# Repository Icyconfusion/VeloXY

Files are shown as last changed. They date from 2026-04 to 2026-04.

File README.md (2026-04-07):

# VeloXY
A CoreXY 3d printer with a heated chamber and bed. It has 300x300x320 print volume and 3 point bed-levelling. I made this project to be able to print higher quality materials. The printer runs Marlin firmware.



## **Assembly**
The assembly is centered around a frame made of galvanised square steel (40x40). The frame is essentially a cube, where the square steel is welded together, so no connectors are needed. Two cross bars at the top are lowered by ~60mm to provide clearance for the extruder and filament path. 



Components are mounted onto the square steel using rivet nuts. 

### Z axis

The Z axis uses 3 independent motors to enable 3 point bed-levelling. At each motor, there is a T8 leadscrew to drive motion, and an 8mm smooth rod for support. The smooth rod is press fit into the 3d printed brackets through small slits in the brackets for compliance. The nema 17 motor mounts to the bracket, and secures the leadscrew with a 5x8 shaft coupler. At the idler, the leadscrew is held in place with a 16x8x5 bearing, allowing rotation. 






The intersection of the corner Nema 17 motors with the square steel is not an error, as a section of the square steel will be cutout (a rectangle just bigger than the motor) so that the motor sits in there without touching any of the steel.

Bed supports hold an LM8UU bearing and a anti-backlash nut. This transfers motion to the bed. The bed sits on these supports through a threaded steel ball (Vcore system) which rests on metal dowels in the bracket.







### Gantry (X and Y)
The gantry is the 2020 T slot profile that moves back and forth along the Y axis. The gantry is supported by two 3d printed brackets, one at each end, that connect it to the MGN12H carriages. The Y linear rails are mounted on the underside of the frame.




 The gantry has a linear rail along the top face of the profile, this is the X axis.

 
 

The extruder runs along this linear rail for the X axis. The extruder is sat on a MGN12H carriage, and holds a nema 17 motor for the extruder and the hotend. Two blower fans cool the nozzle/part.





### Chamber
The chamber is mounted around the frame, aiming to create a closed off area that can be heated for better printing. The enclosure is made up of ACM, mounted on the top, back, bottom and sides using rivet nuts.


A hole is drilled in the back panel so that wires for electronics can enter the chamber.



The enclosure is finished with a polycarbonate door on a hinge mounted to the frame, with a 3d printed handle.



The chamber is heated by a PTC heater in the bottom corner, mounted to a base tube of square steel, and a vertical post using a small metal rectangle with mounting holes drilled.




### Motion
The printer is based on a coreXY motion system. The belts are stacked on top of each other, so there is no need for a crossover system.



There are pulleys on the idlers and belt post on the gantry. The belts connect to a post/screw on the extruder.



## **Electronics**
I designed a PCB motherboard around the mega2560 that will control the printer. The motherboard is 2 layers and uses A4988 footprint drivers. Power for the motors and heaters enters the board with a screw terminal from the 24v 600w PSU. There is also an 5v screw terminal input which powers the motor driver logic, lcd and if needed the arduino. The 5v comes from the psu but with a buck converter between. There is a third power input for the arduino vin pin which can be used if needed, but the arduino can also be powered by the 5v supply and usb. The LCD connects to a 4 pin header, with RX, TX, 5V and GND. All three heaters (Hotend, bed and chamber) are controlled through TO-220 mosfets, but the chamber has its own PSU. There are also fuses for the power inputs.





## **BOM**
**Printed parts**
| Part | Quantity | Picture |
|---|---|---|
| A bottom corner | 1 |
| A bed support | 1 | 
| A idler | 1 |
| A motor | 1 | 
| A gantry belt post | 1 |
| A gantry mount | 1 | 
| B bottom corner | 1 | 
| B bed support | 1 |
| B idler | 1 | 
| B motor | 1 | 
| B gantry belt post | 1 | 
| B gantry mount | 1 | 
| Z front bracket | 1 |
| Front bed support | 1 | 
| Front top support | 1 | 
| Handle | 1 | 
| Extruder | 1 | 
| Electronics case | 1 | 

**Purchased Parts**
|Name |Purpose |Quantity|Total Cost (USD)|Link |Distributor |
|---|---|---|---|---|---|
|Mosfets |IRLB3034PBF MOSFETs for controlling the heaters of the printer. |3 |4.06 |https://www.aliexpress.com/item/4000222160431.html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 |Aliexpress |
|Capacitors |220 uf 50V capacitors for the motherboard |6 |3.80 |https://www.aliexpress.com/item/1005011631970768.html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 |Aliexpress |
|female headers |For connecting the A4988 drivers to the motherboard |12 |5.52 |https://www.aliexpress.com/item/4000059515638.html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 |Aliexpress |
|Male pin headers |For connecting components like endstops and the MCU to the motherboard |1 |8.74 |https://www.aliexpress.com/item/1005011692961056.html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|Aliexpress |
|Blower fan |Cooling the nozzle/part |2 |4.60 |https://www.aliexpress.com/item/1005006744255466.html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 |Aliexpress |
|Bearing |16x8x5 bearing for holding the top of leadscrews in place |3 |0.45 |https://jlcmc.com/product/b/C15/BR8364/deep-groove-ball-bearing-double-side-with-dust-cover |JLCMC |
|Fuse |KCD3 Fuse holder for the motherboard. For the main PSU, 30-35A fuse. For bed PSU, 20A fuse. |2 |7.80 |https://www.aliexpress.com/item/1005005182079397.html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 |Aliexpress |
|Screw terminals  |30A Screw terminals for powering motherboard, and connecting heaters to motherboard |7 |5.52 |https://www.aliexpress.com/item/1005009941526260.html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 |Aliexpress |
|Resistors |1/4 watt, 10k and 150 ohm resistors for the motherboard MOSFETS |6 |5.73 |https://www.aliexpress.com/item/1005008464765307.html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 |Aliexpress |
|Capacitors |100 nf (0.1 uf) 50V ceramic capacitors for the motherboard |6 |0.00 |https://www.aliexpress.com/item/1005006883576409.html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 |Aliexpress |
|Screws |For fastening components to the the rivet nuts. 225 M5, 5 M4, 100 M3 |330 |7.73 |https://jlcmc.com/product/s/E02/EDLA/hex-socket-screw-full-partial-thread-standard-type-(din-912-gb-t-70.1) |JLCMC |
|PEI sheet |The print surface that goes on top of the print bed. 310x310 |1 |14.63 |https://www.aliexpress.com/item/1005006866749353.html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 |Aliexpress |
|Polycarbonate |Polycarbonate sheet for the door. |1 |30.00 |https://www.bunnings.com.au/suntuf-400-x-400-x-8mm-clear-palsun-polycarbonate-sheet-8mm_p1010483 |Bunnings |
|Heat set inserts |Attaching electronics case lid |4 |0.17 |https://jlcmc.com/product/s/E04/EMLU/insert-nut-through-hole |JLCMC |
|Rivet nuts |Nuts for fastening things to the square steel tubing. Need 175 M5, 5 M4, 100 M3 |280 |7.59 |https://jlcmc.com/product/s/E12/EMJE/rivet-nut-pull-through-ribbed-dome-head |JLCMC |
|MK8 extruder |The MK8 extruder pushes filament into the hotend using the Nema 17 motor |1 |4.33 |https://www.aliexpress.com/item/1005007542803374.html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 |Aliexpress |
|PTC heater |The space heater for the heated chamber of the printer to enable printing harder materials. 24v 400w. |1 |17.00 |https://www.aliexpress.com/item/1005007442989854.html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 |Aliexpress |
|Heated bed |300x300 24v heated bed to heat up the print surface |1 |25.00 |https://www.aliexpress.com/item/1005008233590835.html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 |Aliexpress |
|Square steel tube|2mm thick 40x40 Galvanised square steel tubing is the frame for the printer. I will use 40x40 as it has greater strength. I will cut it to length, drill holes where necessary for mounting and then weld together. I will need 6m. |1 |31.06 |https://www.rhssteelsupplies.com.au/hikashop-menu-for-categories-listing/product/3127-galvanised-square-hollow-box-section-40-x-40-x-2-5-gal-8-metres.html |RHS Steel Supplies|
|ACM panel |ACM panel will make the enclosure for the printer. I need to use ACM as it is the cheapest suitable material, as it must be able to contain the heat of the chamber without weakening. I will cut/bend the ACM to fit around the frame.|1 |60.00 |https://plastix.com.au/product/aluminium-composite-panels/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 |Plastix.com.au |

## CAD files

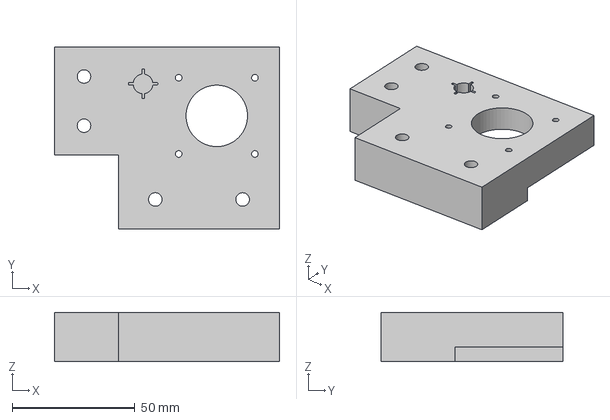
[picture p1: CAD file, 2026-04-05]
CAD/A+corner+bracket.stp
91.5 x 74.0 x 20.0 mm

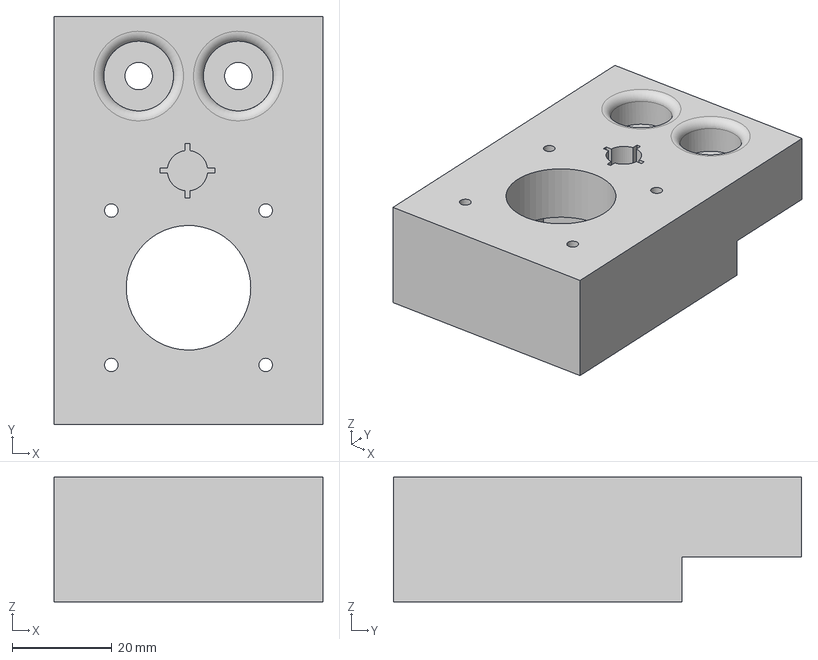
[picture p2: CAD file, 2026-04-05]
CAD/Z+front+bracket.stp
54.0 x 82.0 x 25.0 mm

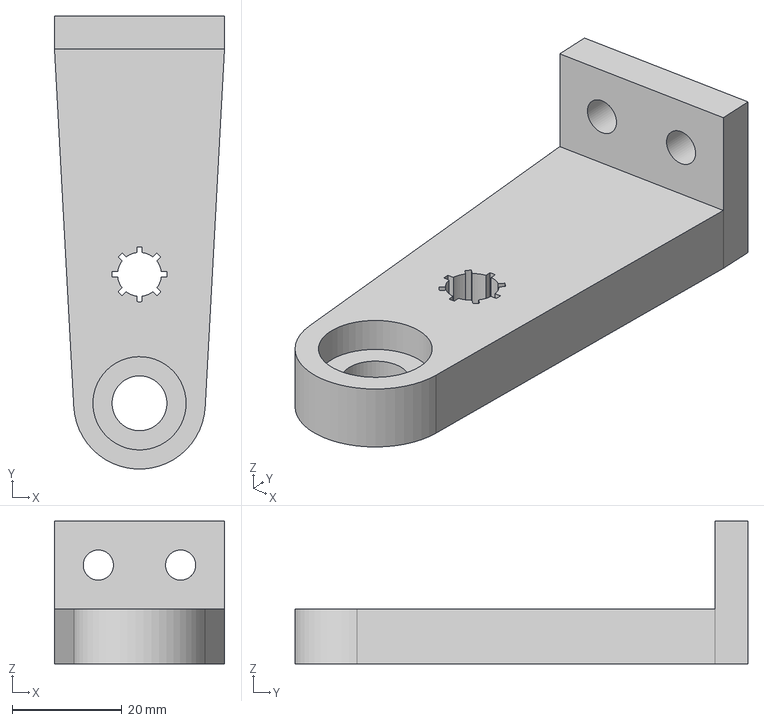
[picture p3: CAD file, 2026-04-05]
CAD/Front+top+support.stp
31.0 x 82.6 x 26.0 mm

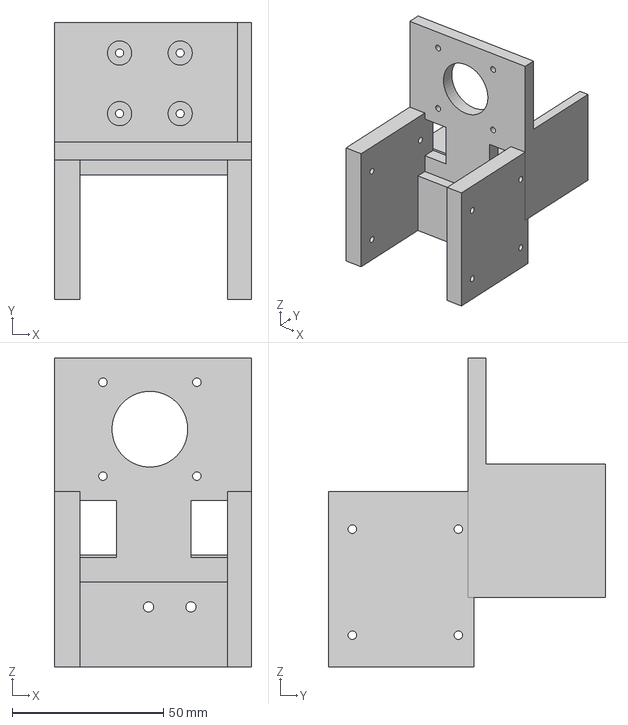
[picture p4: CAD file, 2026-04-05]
CAD/X+carriage.stp
65.0 x 91.3 x 102.0 mm

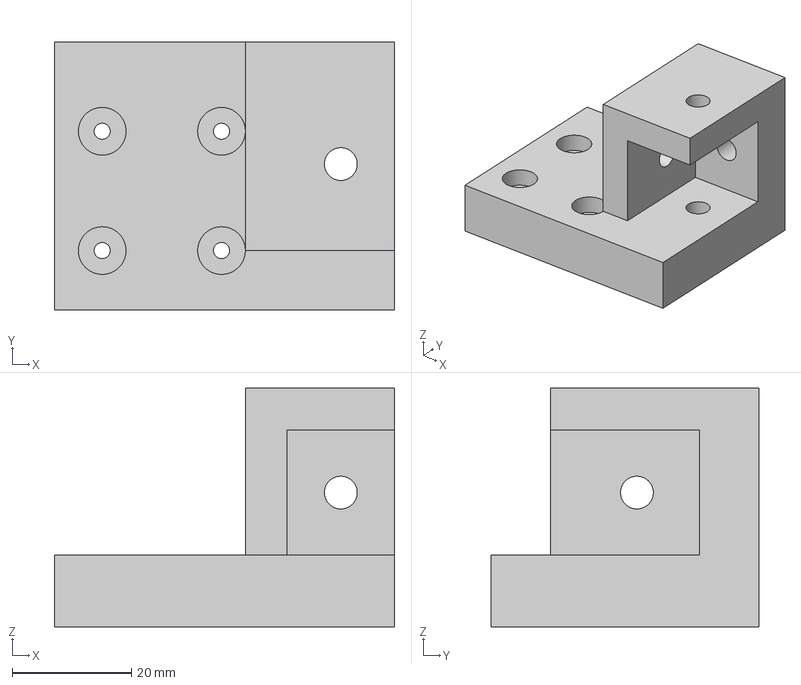
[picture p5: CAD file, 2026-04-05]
CAD/Y+carriage+A.stp
57.0 x 45.0 x 40.0 mm

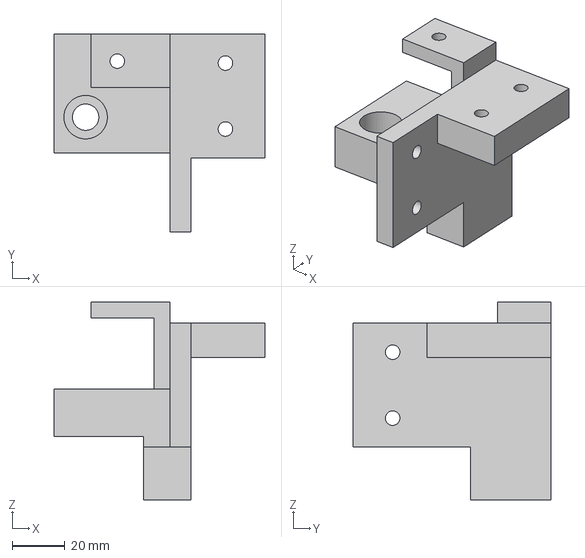
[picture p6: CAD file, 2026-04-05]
CAD/B+idler.stp
80.0 x 75.0 x 75.0 mm

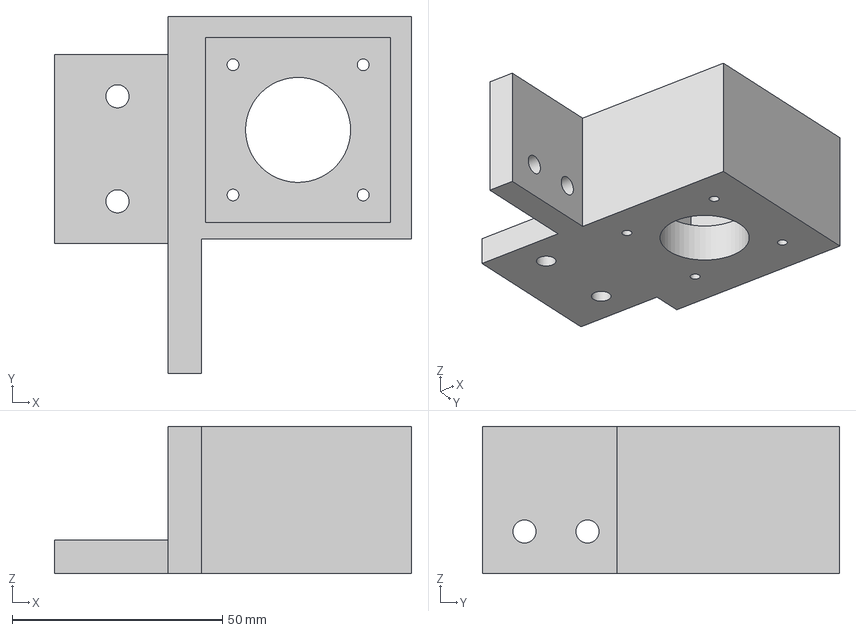
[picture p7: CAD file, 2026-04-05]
CAD/B+motor.stp
85.0 x 85.0 x 35.0 mm

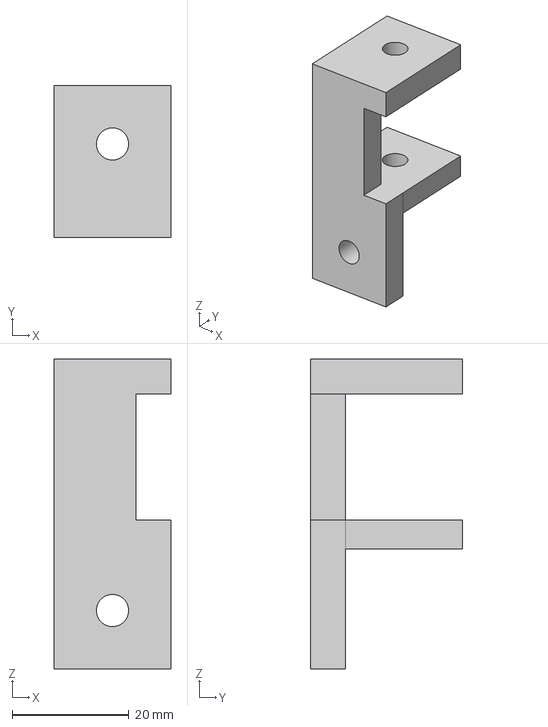
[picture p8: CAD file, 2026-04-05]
CAD/Gantry+belt+post.stp
20.0 x 26.0 x 53.0 mm

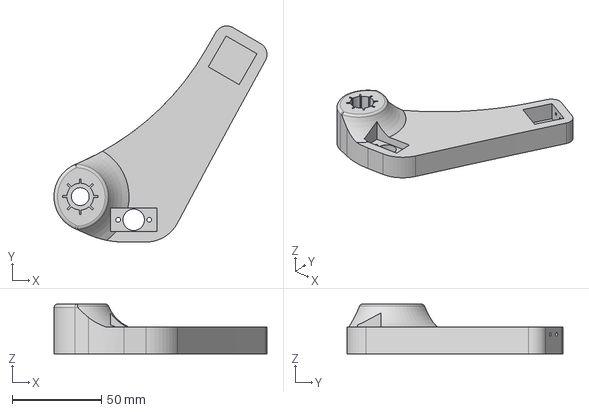
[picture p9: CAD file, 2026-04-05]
CAD/A+bed+support.stp
119.5 x 121.3 x 28.0 mm

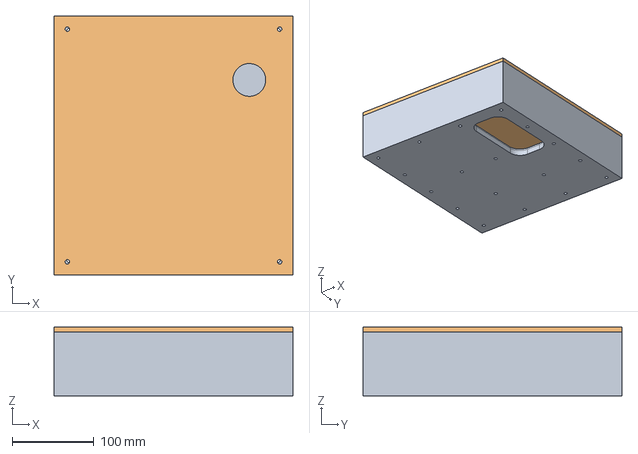
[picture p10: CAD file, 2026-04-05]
CAD/Electronics+case.stp
291.0 x 316.0 x 84.0 mm

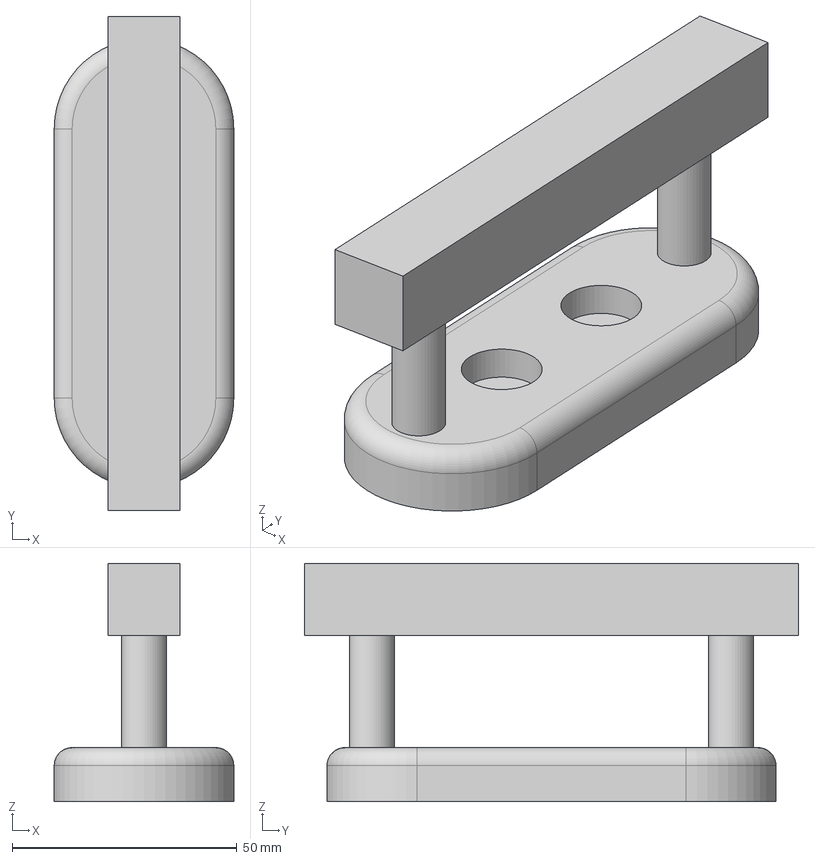
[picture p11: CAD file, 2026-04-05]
CAD/Handle.stp
40.0 x 110.0 x 53.0 mm

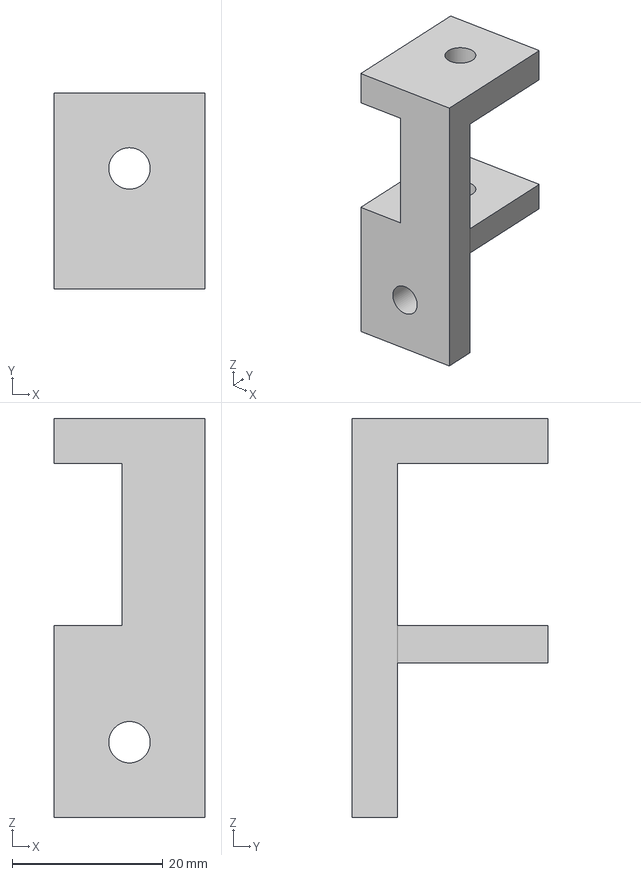
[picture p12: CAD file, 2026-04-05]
CAD/Gantry+belt+post+B.stp
20.0 x 26.0 x 53.0 mm

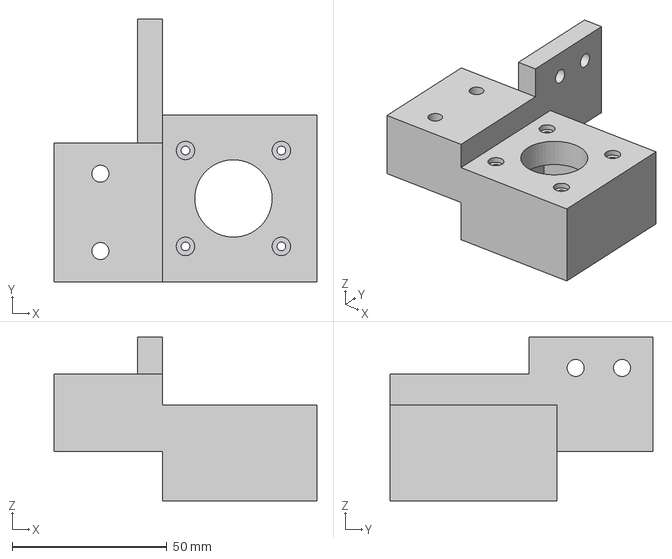
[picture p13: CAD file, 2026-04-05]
CAD/A+motor.stp
85.0 x 85.0 x 53.0 mm

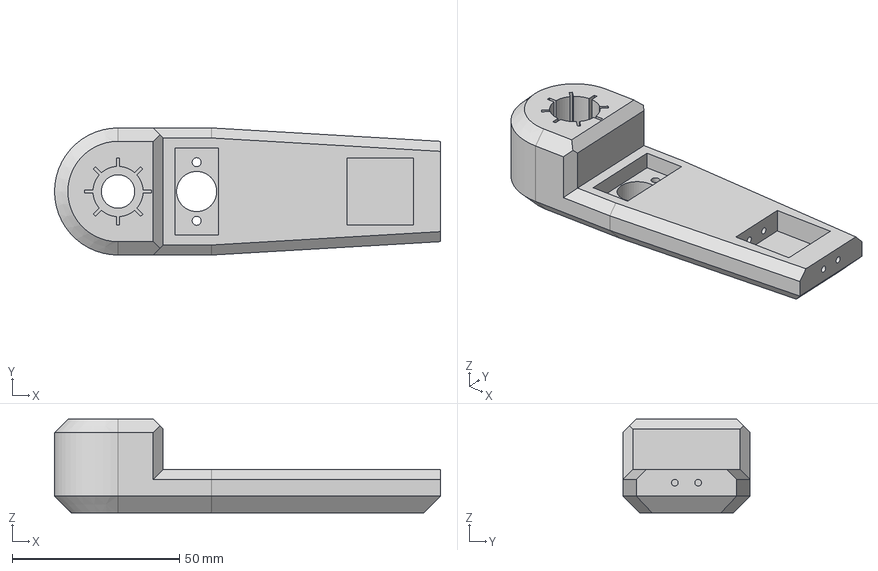
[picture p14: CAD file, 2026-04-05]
CAD/Bed+support+rear.stp
115.4 x 38.0 x 28.0 mm

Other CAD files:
CAD/Assembly (1).stp
CAD/B+corner+bracket.stp
CAD/Y+carriage+B.stp
CAD/B+bed+support+new.stp
CAD/A+idler.stp

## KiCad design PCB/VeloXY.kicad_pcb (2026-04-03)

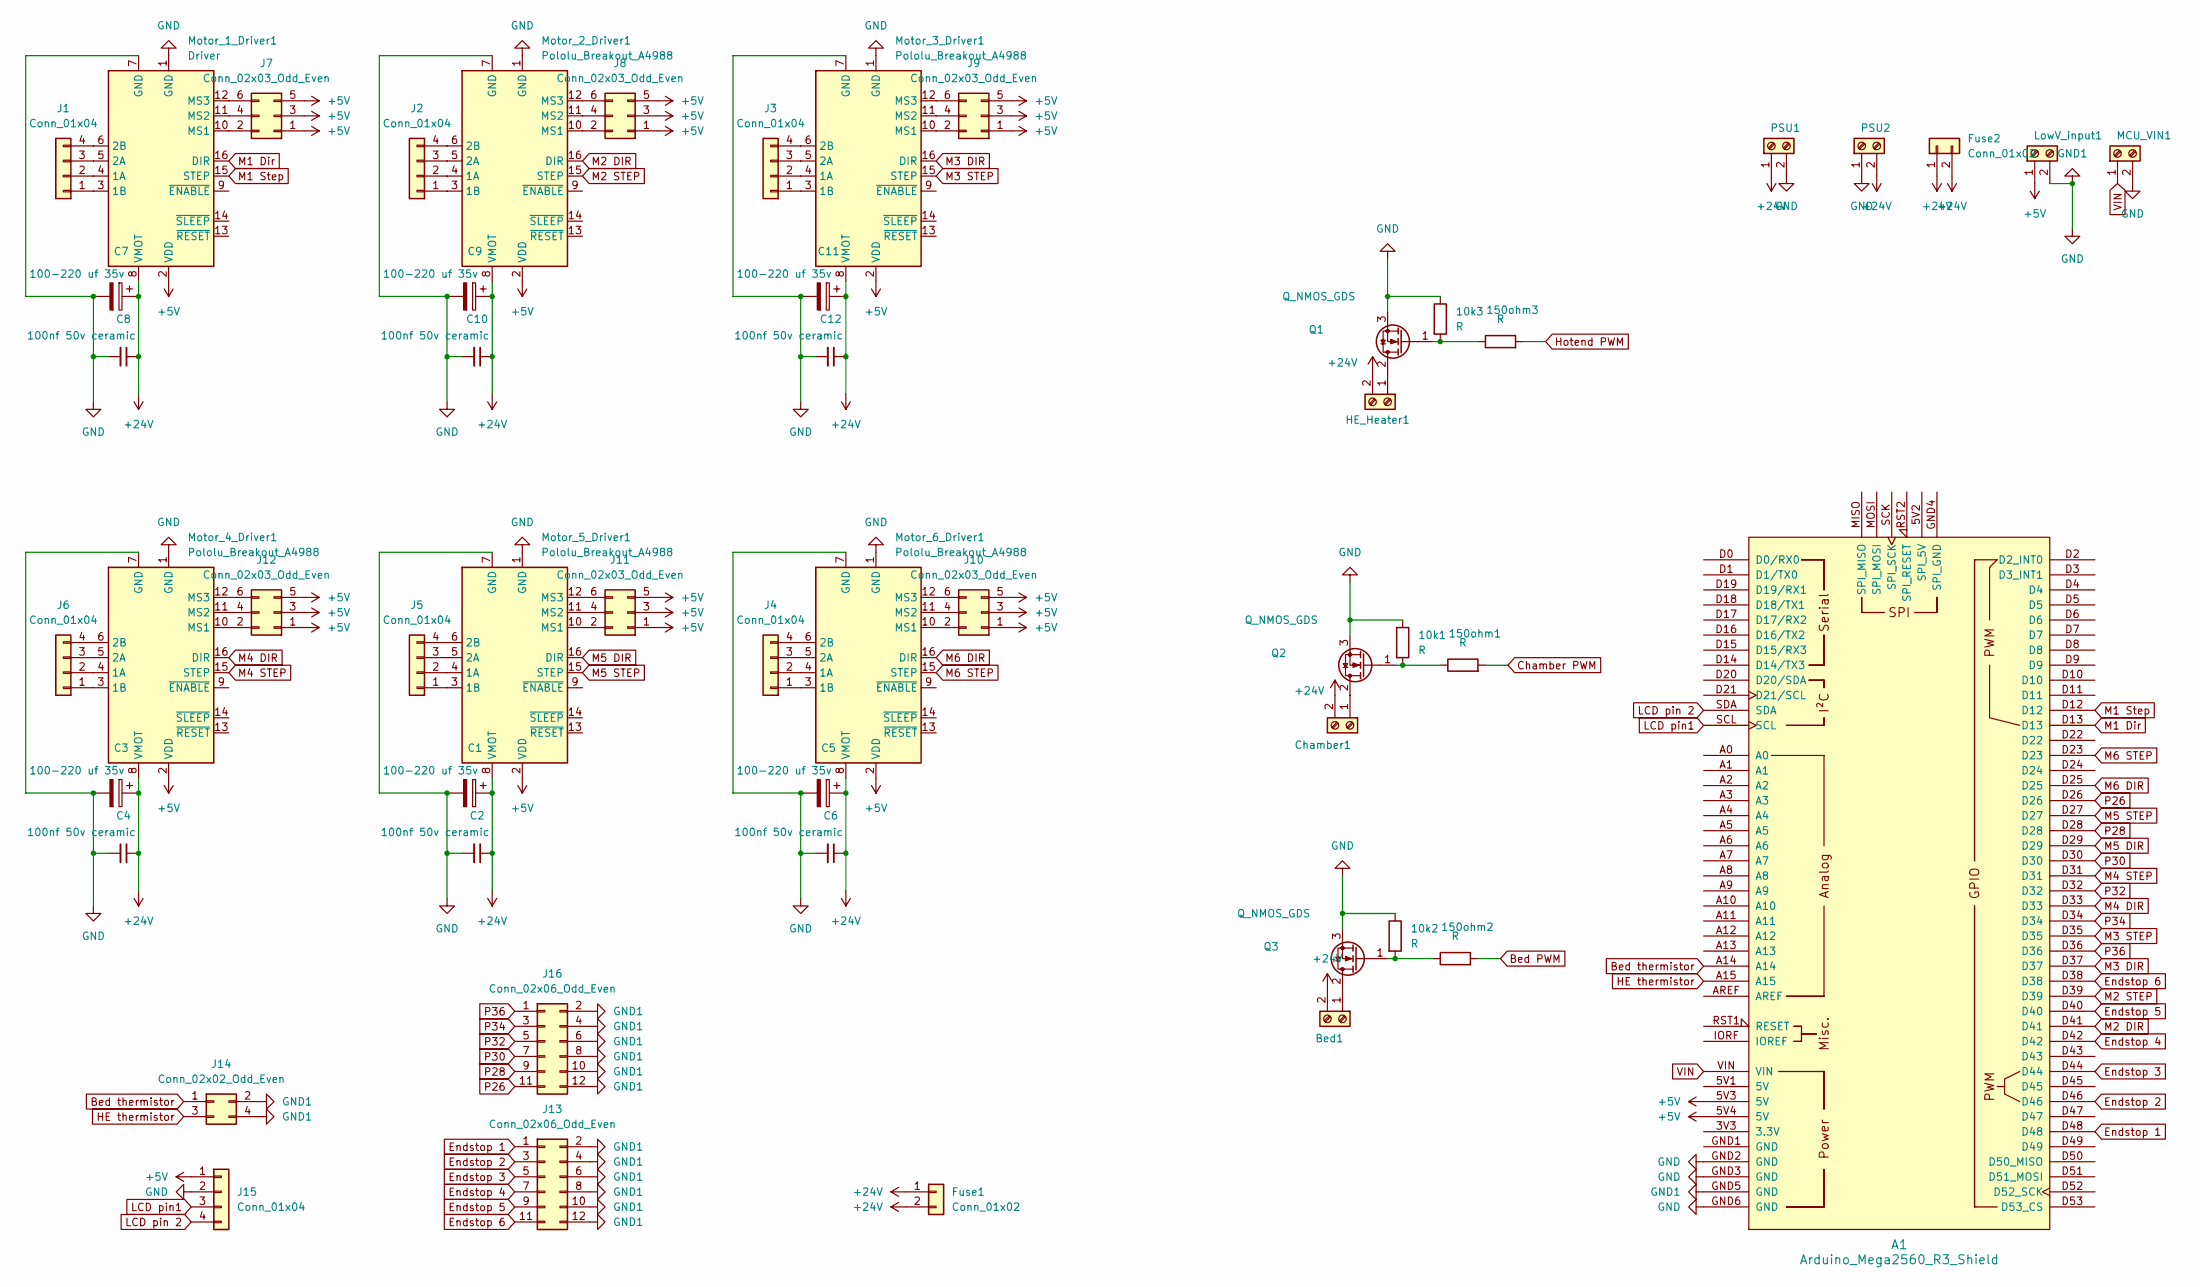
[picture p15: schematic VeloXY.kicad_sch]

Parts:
10k1, 10k2, 10k3, 150ohm1, 150ohm2, 150ohm3: R; R_Axial_DIN0207_L6.3mm_D2.5mm_P7.62mm_Horizontal
A1: Arduino_Mega2560_R3_Shield
Bed1: Screw_Terminal_01x02; Wuerth_691311400102_P7.62mm
C1, C3, C5, C7, C9, C11: 100-220 uf 35v; CP_Radial_D8.0mm_P5.00mm
C2, C4, C6, C8, C10, C12: 100nf 50v ceramic; C_Disc_D5.0mm_W2.5mm_P5.00mm
Chamber1: Screw_Terminal_01x02; Wuerth_691311400102_P7.62mm
Fuse1, Fuse2: Conn_01x02; Fuse_Holder_KCD3_Medium
HE_Heater1: Screw_Terminal_01x02; Wuerth_691311400102_P7.62mm
J1, J2, J3, J4, J5, J6, J15: Conn_01x04; PinHeader_1x04_P2.54mm_Vertical
J7, J8, J9, J10, J11, J12: Conn_02x03_Odd_Even; PinHeader_2x03_P2.54mm_Vertical
J13, J16: Conn_02x06_Odd_Even; PinHeader_2x06_P2.54mm_Vertical
J14: Conn_02x02_Odd_Even; PinHeader_2x02_P2.54mm_Vertical
LowV_input1: Screw_Terminal_01x02; Wuerth_691311400102_P7.62mm
MCU_VIN1: Screw_Terminal_01x02; Wuerth_691311400102_P7.62mm
Motor_1_Driver1: Driver; Pololu_Breakout-16_15.2x20.3mm
Motor_2_Driver1, Motor_3_Driver1, Motor_4_Driver1, Motor_5_Driver1, Motor_6_Driver1: Pololu_Breakout_A4988; Pololu_Breakout-16_15.2x20.3mm
PSU1, PSU2: Screw_Terminal_01x02; Wuerth_691311400102_P7.62mm
Q1, Q2, Q3: Q_NMOS_GDS; TO-220-3_Vertical

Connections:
+5V: A1.5V3 (5V), A1.5V4 (5V), J7.1, J7.3, J7.5, J8.1, J8.3, J8.5, J9.1, J9.3, J9.5, J10.1, J10.3, J10.5, J11.1, J11.3, J11.5, J12.1, J12.3, J12.5, J15.1, LowV_input1.1, Motor_1_Driver1.2 (VDD), Motor_2_Driver1.2 (VDD), Motor_3_Driver1.2 (VDD), Motor_4_Driver1.2 (VDD), Motor_5_Driver1.2 (VDD), Motor_6_Driver1.2 (VDD)
+24V: Bed1.2, C1.1, C2.1, C3.1, C4.1, C5.1, C6.1, C7.1, C8.1, C9.1, C10.1, C11.1, C12.1, Chamber1.2, Fuse1.1, Fuse1.2, Fuse2.1, Fuse2.2, HE_Heater1.2, Motor_1_Driver1.8 (VMOT), Motor_2_Driver1.8 (VMOT), Motor_3_Driver1.8 (VMOT), Motor_4_Driver1.8 (VMOT), Motor_5_Driver1.8 (VMOT), Motor_6_Driver1.8 (VMOT), PSU1.1, PSU2.2
Bed PWM: 150ohm2.2
Bed thermistor: A1.A14, J14.1
Chamber PWM: 150ohm1.2
Endstop 1: A1.D48, J13.1
Endstop 2: A1.D46, J13.3
Endstop 3: A1.D44, J13.5
Endstop 4: A1.D42, J13.7
Endstop 5: A1.D40, J13.9
Endstop 6: A1.D38, J13.11
GND: 10k1.1, 10k2.1, 10k3.1, A1.GND2 (GND), A1.GND3 (GND), A1.GND5 (GND), A1.GND6 (GND), C1.2, C2.2, C3.2, C4.2, C5.2, C6.2, C7.2, C8.2, C9.2, C10.2, C11.2, C12.2, J13.2, J13.4, J13.6, J13.8, J13.10, J13.12, J14.2, J14.4, J15.2, J16.2, J16.4, J16.6, J16.8, J16.10, J16.12, LowV_input1.2, MCU_VIN1.2, Motor_1_Driver1.1 (GND), Motor_1_Driver1.7 (GND), Motor_2_Driver1.1 (GND), Motor_2_Driver1.7 (GND), Motor_3_Driver1.1 (GND), Motor_3_Driver1.7 (GND), Motor_4_Driver1.1 (GND), Motor_4_Driver1.7 (GND), Motor_5_Driver1.1 (GND), Motor_5_Driver1.7 (GND), Motor_6_Driver1.1 (GND), Motor_6_Driver1.7 (GND), PSU1.2, PSU2.1, Q1.3 (S), Q2.3 (S), Q3.3 (S)
HE thermistor: A1.A15, J14.3
Hotend PWM: 150ohm3.2
LCD pin1: A1.SCL, J15.3
LCD pin 2: A1.SDA, J15.4
M1 Dir: A1.D13, Motor_1_Driver1.16 (DIR)
M1 Step: A1.D12, Motor_1_Driver1.15 (STEP)
M2 DIR: A1.D41, Motor_2_Driver1.16 (DIR)
M2 STEP: A1.D39, Motor_2_Driver1.15 (STEP)
M3 DIR: A1.D37, Motor_3_Driver1.16 (DIR)
M3 STEP: A1.D35, Motor_3_Driver1.15 (STEP)
M4 DIR: A1.D33, Motor_4_Driver1.16 (DIR)
M4 STEP: A1.D31, Motor_4_Driver1.15 (STEP)
M5 DIR: A1.D29, Motor_5_Driver1.16 (DIR)
M5 STEP: A1.D27, Motor_5_Driver1.15 (STEP)
M6 DIR: A1.D25, Motor_6_Driver1.16 (DIR)
M6 STEP: A1.D23, Motor_6_Driver1.15 (STEP)
unnamed: Bed1.1, Q3.2 (D)
unnamed: Chamber1.1, Q2.2 (D)
unnamed: HE_Heater1.1, Q1.2 (D)
unnamed: J1.1, Motor_1_Driver1.3 (1B)
unnamed: J1.2, Motor_1_Driver1.4 (1A)
unnamed: J1.3, Motor_1_Driver1.5 (2A)
unnamed: J1.4, Motor_1_Driver1.6 (2B)
unnamed: J2.1, Motor_2_Driver1.3 (1B)
unnamed: J2.2, Motor_2_Driver1.4 (1A)
unnamed: J2.3, Motor_2_Driver1.5 (2A)
unnamed: J2.4, Motor_2_Driver1.6 (2B)
unnamed: J3.1, Motor_3_Driver1.3 (1B)
unnamed: J3.2, Motor_3_Driver1.4 (1A)
unnamed: J3.3, Motor_3_Driver1.5 (2A)
unnamed: J3.4, Motor_3_Driver1.6 (2B)
unnamed: J4.1, Motor_6_Driver1.3 (1B)
unnamed: J4.2, Motor_6_Driver1.4 (1A)
unnamed: J4.3, Motor_6_Driver1.5 (2A)
unnamed: J4.4, Motor_6_Driver1.6 (2B)
unnamed: J5.1, Motor_5_Driver1.3 (1B)
unnamed: J5.2, Motor_5_Driver1.4 (1A)
unnamed: J5.3, Motor_5_Driver1.5 (2A)
unnamed: J5.4, Motor_5_Driver1.6 (2B)
unnamed: J6.1, Motor_4_Driver1.3 (1B)
unnamed: J6.2, Motor_4_Driver1.4 (1A)
unnamed: J6.3, Motor_4_Driver1.5 (2A)
unnamed: J6.4, Motor_4_Driver1.6 (2B)
unnamed: J7.2, Motor_1_Driver1.10 (MS1)
unnamed: J7.4, Motor_1_Driver1.11 (MS2)
unnamed: J7.6, Motor_1_Driver1.12 (MS3)
unnamed: J8.2, Motor_2_Driver1.10 (MS1)
unnamed: J8.4, Motor_2_Driver1.11 (MS2)
unnamed: J8.6, Motor_2_Driver1.12 (MS3)
unnamed: J9.2, Motor_3_Driver1.10 (MS1)
unnamed: J9.4, Motor_3_Driver1.11 (MS2)
unnamed: J9.6, Motor_3_Driver1.12 (MS3)
unnamed: J10.2, Motor_6_Driver1.10 (MS1)
unnamed: J10.4, Motor_6_Driver1.11 (MS2)
unnamed: J10.6, Motor_6_Driver1.12 (MS3)
unnamed: J11.2, Motor_5_Driver1.10 (MS1)
unnamed: J11.4, Motor_5_Driver1.11 (MS2)
unnamed: J11.6, Motor_5_Driver1.12 (MS3)
unnamed: J12.2, Motor_4_Driver1.10 (MS1)
unnamed: J12.4, Motor_4_Driver1.11 (MS2)
unnamed: J12.6, Motor_4_Driver1.12 (MS3)
unnamed: 10k3.2, 150ohm3.1, Q1.1 (G)
unnamed: 10k1.2, 150ohm1.1, Q2.1 (G)
unnamed: 10k2.2, 150ohm2.1, Q3.1 (G)
P26: A1.D26, J16.11
P28: A1.D28, J16.9
P30: A1.D30, J16.7
P32: A1.D32, J16.5
P34: A1.D34, J16.3
P36: A1.D36, J16.1
VIN: A1.VIN, MCU_VIN1.1

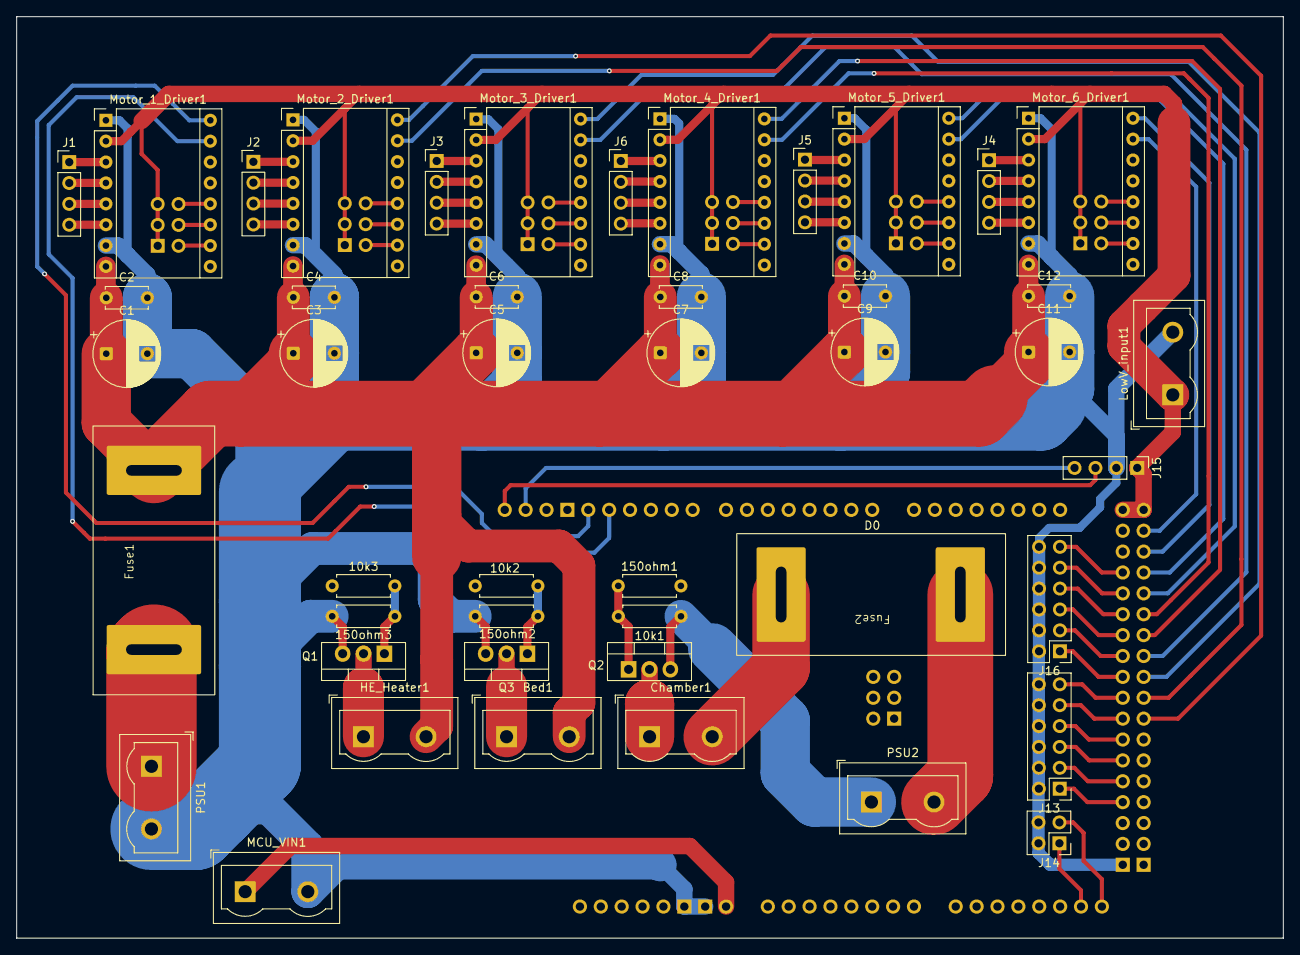
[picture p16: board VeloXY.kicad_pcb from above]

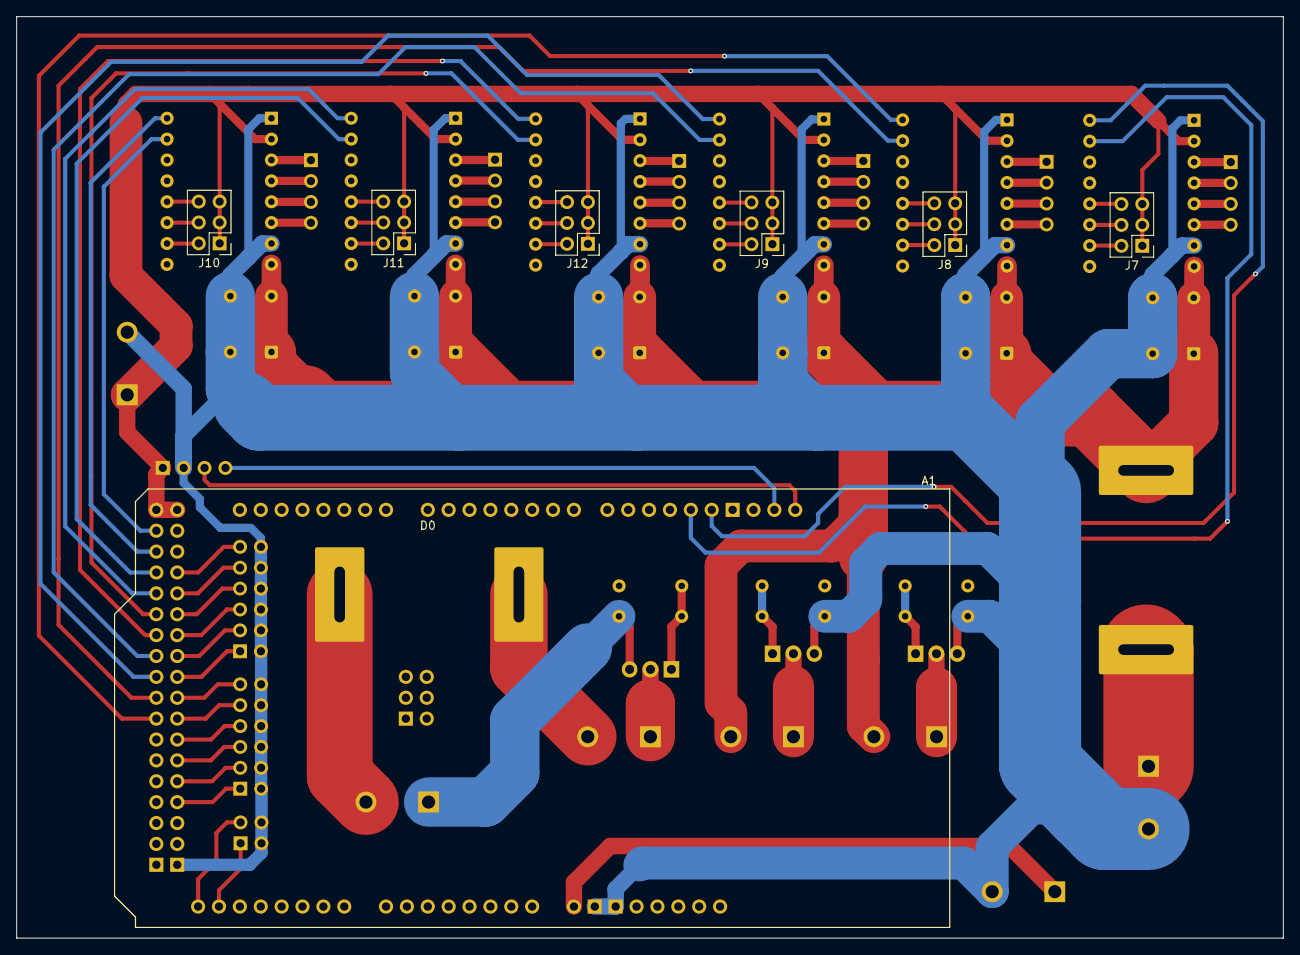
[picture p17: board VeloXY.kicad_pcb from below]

Board: 2 copper layers, 154.1 x 112.1 mm, 53 parts (6 on the bottom side), 80 nets.

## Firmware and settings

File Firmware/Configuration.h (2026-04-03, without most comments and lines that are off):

#pragma once
#define CONFIGURATION_H_VERSION 02010206
#define STRING_CONFIG_H_AUTHOR "(none, default config)" // Who made the changes.
#define SHOW_BOOTSCREEN
  #define MOTHERBOARD BOARD_RAMPS_14_EFB
#define SERIAL_PORT 0
#define BAUDRATE 250000
#define X_DRIVER_TYPE  A4988
#define Y_DRIVER_TYPE  A4988
#define Z_DRIVER_TYPE  A4988
#define E0_DRIVER_TYPE A4988
#define EXTRUDERS 1
#define DEFAULT_NOMINAL_FILAMENT_DIA 1.75
#define TEMP_SENSOR_0 1
#define TEMP_SENSOR_1 0
#define TEMP_SENSOR_2 0
#define TEMP_SENSOR_3 0
#define TEMP_SENSOR_4 0
#define TEMP_SENSOR_5 0
#define TEMP_SENSOR_6 0
#define TEMP_SENSOR_7 0
#define TEMP_SENSOR_BED 1
#define TEMP_SENSOR_PROBE 0
#define TEMP_SENSOR_CHAMBER 0
#define TEMP_SENSOR_COOLER 0
#define TEMP_SENSOR_BOARD 0
#define TEMP_SENSOR_REDUNDANT 0
#define DUMMY_THERMISTOR_998_VALUE  25
#define DUMMY_THERMISTOR_999_VALUE 100
#if TEMP_SENSOR_IS_MAX_TC(0)
  #define MAX31865_SENSOR_OHMS_0      100 // (Ω) Typically 100 or 1000 (PT100 or PT1000)
  #define MAX31865_CALIBRATION_OHMS_0 430 // (Ω) Typically 430 for Adafruit PT100; 4300 for Adafruit PT1000
#endif
#if TEMP_SENSOR_IS_MAX_TC(1)
  #define MAX31865_SENSOR_OHMS_1      100
  #define MAX31865_CALIBRATION_OHMS_1 430
#endif
#if TEMP_SENSOR_IS_MAX_TC(2)
  #define MAX31865_SENSOR_OHMS_2      100
  #define MAX31865_CALIBRATION_OHMS_2 430
#endif
#if HAS_E_TEMP_SENSOR
  #define TEMP_RESIDENCY_TIME         10  // (seconds) Time to wait for hotend to "settle" in M109
  #define TEMP_WINDOW                  1  // (°C) Temperature proximity for the "temperature reached" timer
  #define TEMP_HYSTERESIS              3  // (°C) Temperature proximity considered "close enough" to the target
#endif
#if TEMP_SENSOR_BED
  #define TEMP_BED_RESIDENCY_TIME     10  // (seconds) Time to wait for bed to "settle" in M190
  #define TEMP_BED_WINDOW              1  // (°C) Temperature proximity for the "temperature reached" timer
  #define TEMP_BED_HYSTERESIS          3  // (°C) Temperature proximity considered "close enough" to the target
#endif
#if TEMP_SENSOR_CHAMBER
  #define TEMP_CHAMBER_RESIDENCY_TIME 10  // (seconds) Time to wait for chamber to "settle" in M191
  #define TEMP_CHAMBER_WINDOW          1  // (°C) Temperature proximity for the "temperature reached" timer
  #define TEMP_CHAMBER_HYSTERESIS      3  // (°C) Temperature proximity considered "close enough" to the target
#endif
#if TEMP_SENSOR_REDUNDANT
  #define TEMP_SENSOR_REDUNDANT_SOURCE    E1  // The sensor that will provide the redundant reading.
  #define TEMP_SENSOR_REDUNDANT_TARGET    E0  // The sensor that we are providing a redundant reading for.
  #define TEMP_SENSOR_REDUNDANT_MAX_DIFF  10  // (°C) Temperature difference that will trigger a print abort.
#endif
#define HEATER_0_MINTEMP   5
#define HEATER_1_MINTEMP   5
#define HEATER_2_MINTEMP   5
#define HEATER_3_MINTEMP   5
#define HEATER_4_MINTEMP   5
#define HEATER_5_MINTEMP   5
#define HEATER_6_MINTEMP   5
#define HEATER_7_MINTEMP   5
#define BED_MINTEMP        5
#define CHAMBER_MINTEMP    5
#define HEATER_0_MAXTEMP 275
#define HEATER_1_MAXTEMP 275
#define HEATER_2_MAXTEMP 275
#define HEATER_3_MAXTEMP 275
#define HEATER_4_MAXTEMP 275
#define HEATER_5_MAXTEMP 275
#define HEATER_6_MAXTEMP 275
#define HEATER_7_MAXTEMP 275
#define BED_MAXTEMP      150
#define CHAMBER_MAXTEMP  60
#define HOTEND_OVERSHOOT 15   // (°C) Forbid temperatures over MAXTEMP - OVERSHOOT
#define BED_OVERSHOOT    10   // (°C) Forbid temperatures over MAXTEMP - OVERSHOOT
#define COOLER_OVERSHOOT  2   // (°C) Forbid temperatures closer than OVERSHOOT
#define PIDTEMP           // See the PID Tuning Guide at https://reprap.org/wiki/PID_Tuning
#define PID_MAX  255      // Limit hotend current while PID is active (see PID_FUNCTIONAL_RANGE below); 255=full current
#define PID_K1     0.95   // Smoothing factor within any PID loop
    #define DEFAULT_KP  22.20
    #define DEFAULT_KI   1.08
    #define DEFAULT_KD 114.00
#define MAX_BED_POWER 255 // limits duty cycle to bed; 255=full current
#define MAX_CHAMBER_POWER 255 // limits duty cycle to chamber heater; 255=full current
  #define PID_FUNCTIONAL_RANGE 10 // If the temperature difference between the target temperature and the actual temperature
#define PREVENT_COLD_EXTRUSION
#define EXTRUDE_MINTEMP 170
#define PREVENT_LENGTHY_EXTRUDE
#define EXTRUDE_MAXLENGTH 200
#define THERMAL_PROTECTION_HOTENDS // Enable thermal protection for all extruders
#define THERMAL_PROTECTION_BED     // Enable thermal protection for the heated bed
#define THERMAL_PROTECTION_CHAMBER // Enable thermal protection for the heated chamber
#define THERMAL_PROTECTION_COOLER  // Enable thermal protection for the laser cooling
#define USE_XMIN_PLUG
#define USE_YMIN_PLUG
#define USE_ZMIN_PLUG
#define ENDSTOPPULLUPS
#define X_MIN_ENDSTOP_INVERTING false // Set to true to invert the logic of the endstop.
#define Y_MIN_ENDSTOP_INVERTING false // Set to true to invert the logic of the endstop.
#define Z_MIN_ENDSTOP_INVERTING false // Set to true to invert the logic of the endstop.
#define I_MIN_ENDSTOP_INVERTING false // Set to true to invert the logic of the endstop.
#define J_MIN_ENDSTOP_INVERTING false // Set to true to invert the logic of the endstop.
#define K_MIN_ENDSTOP_INVERTING false // Set to true to invert the logic of the endstop.
#define U_MIN_ENDSTOP_INVERTING false // Set to true to invert the logic of the endstop.
#define V_MIN_ENDSTOP_INVERTING false // Set to true to invert the logic of the endstop.
#define W_MIN_ENDSTOP_INVERTING false // Set to true to invert the logic of the endstop.
#define X_MAX_ENDSTOP_INVERTING false // Set to true to invert the logic of the endstop.
#define Y_MAX_ENDSTOP_INVERTING false // Set to true to invert the logic of the endstop.
#define Z_MAX_ENDSTOP_INVERTING false // Set to true to invert the logic of the endstop.
#define I_MAX_ENDSTOP_INVERTING false // Set to true to invert the logic of the endstop.
#define J_MAX_ENDSTOP_INVERTING false // Set to true to invert the logic of the endstop.
#define K_MAX_ENDSTOP_INVERTING false // Set to true to invert the logic of the endstop.
#define U_MAX_ENDSTOP_INVERTING false // Set to true to invert the logic of the endstop.
#define V_MAX_ENDSTOP_INVERTING false // Set to true to invert the logic of the endstop.
#define W_MAX_ENDSTOP_INVERTING false // Set to true to invert the logic of the endstop.
#define Z_MIN_PROBE_ENDSTOP_INVERTING false // Set to true to invert the logic of the probe.
#define DEFAULT_AXIS_STEPS_PER_UNIT   { 80, 80, 400, 500 }
#define DEFAULT_MAX_FEEDRATE          { 300, 300, 5, 25 }
#define DEFAULT_MAX_ACCELERATION      { 3000, 3000, 100, 10000 }
#define DEFAULT_ACCELERATION          3000    // X, Y, Z and E acceleration for printing moves
#define DEFAULT_RETRACT_ACCELERATION  3000    // E acceleration for retracts
#define DEFAULT_TRAVEL_ACCELERATION   3000    // X, Y, Z acceleration for travel (non printing) moves
#define DEFAULT_EJERK    5.0  // May be used by Linear Advance
  #define JUNCTION_DEVIATION_MM 0.013 // (mm) Distance from real junction edge
  #define JD_HANDLE_SMALL_SEGMENTS    // Use curvature estimation instead of just the junction angle
#define Z_MIN_PROBE_USES_Z_MIN_ENDSTOP_PIN
#define NOZZLE_TO_PROBE_OFFSET { 10, 10, 0 }
#define PROBING_MARGIN 10
#define XY_PROBE_FEEDRATE (133*60)
#define Z_PROBE_FEEDRATE_FAST (4*60)
#define Z_PROBE_FEEDRATE_SLOW (Z_PROBE_FEEDRATE_FAST / 2)
#define Z_CLEARANCE_DEPLOY_PROBE   10 // (mm) Z Clearance for Deploy/Stow
#define Z_CLEARANCE_BETWEEN_PROBES  5 // (mm) Z Clearance between probe points
#define Z_CLEARANCE_MULTI_PROBE     5 // (mm) Z Clearance between multiple probes
#define Z_PROBE_LOW_POINT          -2 // (mm) Farthest distance below the trigger-point to go before stopping
#define Z_PROBE_OFFSET_RANGE_MIN -20
#define Z_PROBE_OFFSET_RANGE_MAX 20
#define X_ENABLE_ON 0
#define Y_ENABLE_ON 0
#define Z_ENABLE_ON 0
#define E_ENABLE_ON 0 // For all extruders
#define DISABLE_OTHER_EXTRUDERS   // Keep only the active extruder enabled
#define INVERT_X_DIR false
#define INVERT_Y_DIR true
#define INVERT_Z_DIR false
#define INVERT_E0_DIR false
#define INVERT_E1_DIR false
#define INVERT_E2_DIR false
#define INVERT_E3_DIR false
#define INVERT_E4_DIR false
#define INVERT_E5_DIR false
#define INVERT_E6_DIR false
#define INVERT_E7_DIR false
#define X_HOME_DIR -1
#define Y_HOME_DIR -1
#define Z_HOME_DIR -1
#define X_BED_SIZE 200
#define Y_BED_SIZE 200
#define X_MIN_POS 0
#define Y_MIN_POS 0
#define Z_MIN_POS 0
#define X_MAX_POS X_BED_SIZE
#define Y_MAX_POS Y_BED_SIZE
#define Z_MAX_POS 200
#define MIN_SOFTWARE_ENDSTOPS
  #define MIN_SOFTWARE_ENDSTOP_X
  #define MIN_SOFTWARE_ENDSTOP_Y
  #define MIN_SOFTWARE_ENDSTOP_Z
  #define MIN_SOFTWARE_ENDSTOP_I
  #define MIN_SOFTWARE_ENDSTOP_J
  #define MIN_SOFTWARE_ENDSTOP_K
  #define MIN_SOFTWARE_ENDSTOP_U
  #define MIN_SOFTWARE_ENDSTOP_V
  #define MIN_SOFTWARE_ENDSTOP_W
#define MAX_SOFTWARE_ENDSTOPS
  #define MAX_SOFTWARE_ENDSTOP_X
  #define MAX_SOFTWARE_ENDSTOP_Y
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

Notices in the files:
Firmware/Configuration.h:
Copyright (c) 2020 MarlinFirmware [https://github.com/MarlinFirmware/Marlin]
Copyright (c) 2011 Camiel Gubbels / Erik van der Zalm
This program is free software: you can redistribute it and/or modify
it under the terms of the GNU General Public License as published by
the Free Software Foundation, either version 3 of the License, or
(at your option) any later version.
